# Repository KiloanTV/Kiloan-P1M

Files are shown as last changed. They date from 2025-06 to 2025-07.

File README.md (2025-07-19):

<div>
  <h1 align="center">Kiloan P1M V1</h1>

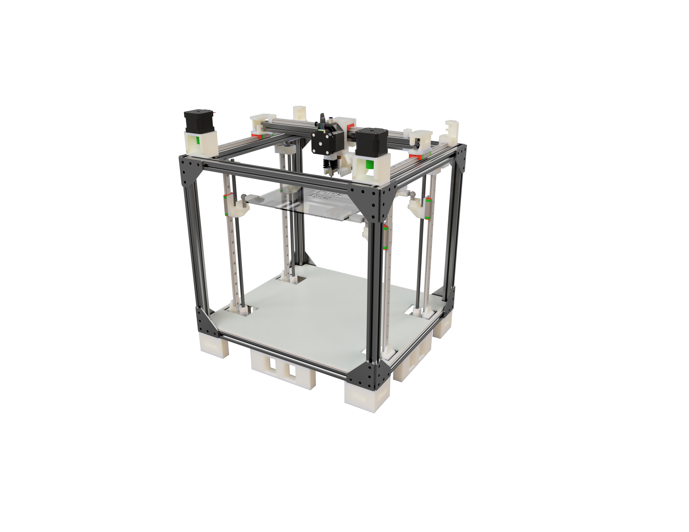
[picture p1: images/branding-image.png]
Kiloan-P1M
  

  <p align="center">
  <a href="https://hackclub.com/highway">
    
  </a>
  </p>
  <h1></h1>
  <p align="center">
    A custom 3D Printer, that is expandable, reliable and can be easily modified!
  </p>
</div>

<sub align="center">This work is licensed under the
[MIT License](https://mit-license.org).
</sub>

## Table of Contents

- [About](#about)
- [Pictures](#pictures)
- [Bill of Materials](#bill-of-materials)

# About

I bought a 3D printer exactly a year ago, and since then, the whole thing has been on my mind. From modeling to the finished part, whether it's spare parts or small gifts. I received an email from GitHub Education informing me about Highway by Hackclub, and after stumbling across it again, I started designing a Corexy 3D printer. Admittedly, it's a bit overkill, but that makes the whole thing even better and allows for many updates. After Highway, I plan to perfect this printer and turn it into a 3D printing/laser cutting combo.

# Pictures

zy

full-printer

# Bill of Materials

|Titel |Quantity|Price in Euro|Shipping costs|Link |
|---|---|---|---|---|
|Aluminium Extrusion 400mm |5 |€13,53 | |https://www.aluxprofil.de/aluminium-nutprofil-2020-v-slot/a3663 |
|Aluminium Extrusion 390mm |4 |€10,53 | |https://www.aluxprofil.de/aluminium-nutprofil-2020-v-slot/a3663 |
|Aluminium Extrusion 350mm |4 |€9,45 | |https://www.aluxprofil.de/aluminium-nutprofil-2020-v-slot/a3663 |
|Aluminium Extrusion 310mm |2 |€4,18 | |https://www.aluxprofil.de/aluminium-nutprofil-2020-v-slot/a3663 |
|Aluminium Extrusion 370mm |1 |€2,50 | |https://www.aluxprofil.de/aluminium-nutprofil-2020-v-slot/a3663 |
|Aluminium Extrusion 80mm (2x40mm) |2 |€1,08 | |https://www.aluxprofil.de/aluminium-nutprofil-2020-v-slot/a3663 |
|Aluminum L-connector plate 60x60 |16 |€19,48 | |https://www.aluxprofil.de/aluminium-l-verbinderplatte-60x60/a3809 |
|Aluminum connector plate 20x80 |4 |€3,39 | |https://www.aluxprofil.de/aluminium-verbinderplatte-20x80/a3804 |
|Washers |4 |1,60€ |5,95€ |https://www.reichelt.de/de/de/shop/produkt/unterlegscheiben_5_3_mm_100_stueck-65765 |
|Miniature ball bearing 698 2RS 8x19x6 mm|4 |2,95€ |2,49€ |https://www.kugellager-express.de/miniatur-kugellager-698-2rs-8x19x6-mm |
|5mm - 8mm Flexible coupling 18x25mm |4 |6,19€ | |https://www.amazon.de/Kupplung-Flexible-Kupplungen-Durchmesser-Maschine/dp/B06WRN9479 |
|350mm linear guides + carriage |4 |53,99€ | |https://www.amazon.de/CNCMANS-Linearf%C3%BChrungen-Schienenf%C3%BChrung-Gleitbl%C3%B6cke-Linearlager/dp/B0BPS1LFH9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 |
|M3 x 12mm Screws |1 pack  |1,69€ |5,90€ |https://www.schraubenking-shop.de/M3-x-12mm-Linsenkopfschrauben-TX-DIN7985-Edelstahl-A2-P004389 |
|M3 Nuts |1 pack  |1,43€ | |https://www.schraubenking-shop.de/M3-Sechskantmuttern-DIN934-Edelstahl-A2-P000447 |
|Nema 17 Steppers |2 x 3 |32,14€ |6,08€ |https://www.omc-stepperonline.com/de/3-stueck-e-serie-nema-17-bipolar-42-ncm-59-49-oz-in-1-5a-42x42x38mm-4-draehte-3-17he15-1504s |
|M3 x 8mm Screws |1 pack  |1,97€ | |https://www.schraubenking-shop.de/M3-x-8mm-Linsenkopfschrauben-TX-DIN7985-Edelstahl-A2-P004281 |
|TR8x4 trapezoidal thread spindle 400mm  |4 |38,40€ | |https://3d-druckershop.com/p/tr8x4-trapezgewindespindel-edelstahl-8mm-laenge-400mm-kaufen |
|TR8x4 trapezoidal thread nut |4 |11,80€ |5,99€ |https://3d-druckershop.com/p/tr8x4-trapezgewindemutter-messing-kaufen |
|M3 x 8mm threaded pin |1 pack  |0,74€ | |https://www.schraubenking-shop.de/M3-x-8mm-Gewindestift-Kegelkuppe-DIN913-Edelstahl-A2-P005088 |
|Miniature ball bearing 608 2RS 8x22x7 mm|4 |2,76€ | |https://www.kugellager-express.de/miniatur-kugellager-608-2rs-8x22x7-mm |
|M5 x 16mm Screws |1 pack  |0,96€ | |https://www.schraubenking-shop.de/M5-x-16mm-Linsenkopfschrauben-TX-DIN7985-Edelstahl-A2-P004003 |
|225mm x 225mm hotbed + aluminium plate  |1 |29,99€ |5,79€ |https://www.3djake.de/elegoo/heizbett-8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 |
|300 mm linear rail guide + carriage |1 x 2 |36,99€ | |https://www.amazon.de/Linearschienenf%C3%BChrung-Lagerstahl-Gleitf%C3%BChrung-Gleitbl%C3%B6cken-CNC-Maschine/dp/B09ZPHPB5F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 |
|MGN12H 350mm linear guide |1 |16,02€ | |https://www.amazon.de/CNCMANS-Linearf%C3%BChrung-Schienenf%C3%BChrung-CNC-Maschine-automatische/dp/B0BG29BQ6H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 |
|M5 angle joint |4 |7,56€ |1,80€ |https://www.ebay.de/itm/124341250847?itemid=124341250847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 |
|M3 x 40mm Screws |1 pack  |3,07€ | |https://www.schraubenking-shop.de/M3-x-40mm-Linsenkopfschrauben-PH-DIN7985-Stahl-verzinkt-FKL48-P002826 |
|Flanged ball bearings |12 |25,99€ | |https://www.kugellager-express.de/miniatur-flanschkugellager-f-695-2rs-5x13x4-mm |
|GT2 pulley idler |2 |5,10€ | |https://www.roboter-bausatz.de/p/gt2-riemenscheibe-idler-20-zaehne-5mm-bohrung-fuer-6mm-schwarz |
|GT2 pulley |2 |1,98€ | |https://www.roboter-bausatz.de/p/gt2-riemenscheibe-20-zaehne-5mm-bohrung-fuer-6mm-riemen |
|M5 x 40mm Screws |1 pack  |1,31€ | |https://www.schraubenking-shop.de/M5-x-40mm-Linsenkopfschrauben-TX-DIN7985-Edelstahl-A2-P004001 |
|M5 x 30mm Screws |1 pack  |1,10€ | |https://www.schraubenking-shop.de/M5-x-30mm-Linsenkopfschrauben-TX-DIN7985-Edelstahl-A2-P004403 |
|Dual Gear Extruder BMG Clone |1 |19,95€ | |https://www.roboter-bausatz.de/p/dual-gear-extruder-bmg-klon-fuer-1.75mm-filament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 |
|Nema 17 Stepper 23mm for extruder |1 |6,53€ | |https://www.omc-stepperonline.com/de/e-serie-nema-17-bipolar-1-8deg-17ncm-24-07oz-in-1a-42x42x23mm-4-draehte-17he08-1004s |
|Bambu X1C Hotend |1 |36,99€ | |https://eu.store.bambulab.com/products/bambu-hotends?id=49242578223452 |
|BL Touch |1 |39,90€ | |https://www.3dprima.com/de/parts/bltouch_23625_4704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 |
|Part cooling fan 5015 24V |1 |1,95€ | |https://www.roboter-bausatz.de/p/radialluefter-5015-24v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 |
|BigTreeTech SKR Mini E3 V3 |2 |0,00€ | |have it already |
|powersupply |1 |45,99€ | |https://www.amazon.de/MEISHILE-Schaltnetzteil-Stromversorgung-Transformator-Spannungswandler/dp/B0DJQRZ24G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 |
|Mainboard fan |2 |0,00€ | |have it already |
|T-Nut 6 M5 for aluminium extrusions |200 |10,09€ | |https://de.aliexpress.com/item/1005007843353724.html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 |
|M5 x 8mm |2 packs |5,62€ | |https://www.schraubenking-shop.de/M5-x-8mm-Linsenkopfschrauben-PH-DIN7985-Stahl-verzinkt-FKL48-P003609 |
|GT2 6mm belt |5 Meter |4,84€ | |https://de.aliexpress.com/item/32921042288.html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|
|||555,73€ or 647,60 USD|||

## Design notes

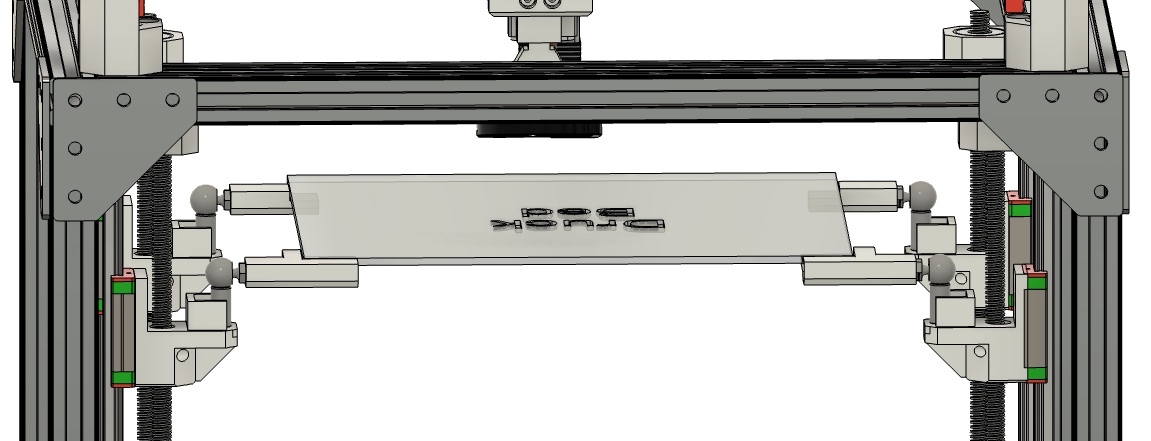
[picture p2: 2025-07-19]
images/bed-system.jpeg

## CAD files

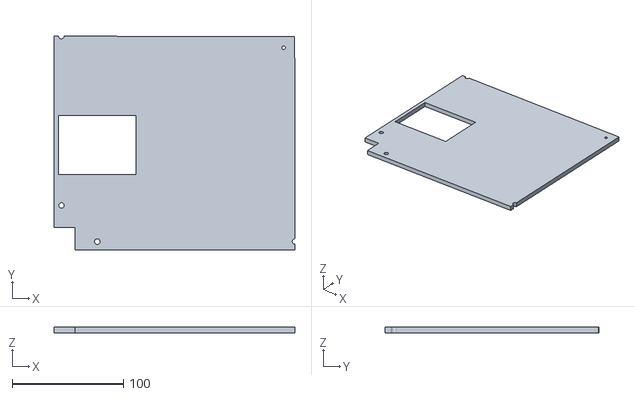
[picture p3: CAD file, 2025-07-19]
hardware/misc/cover2.stl
217.0 x 192.5 x 5.00

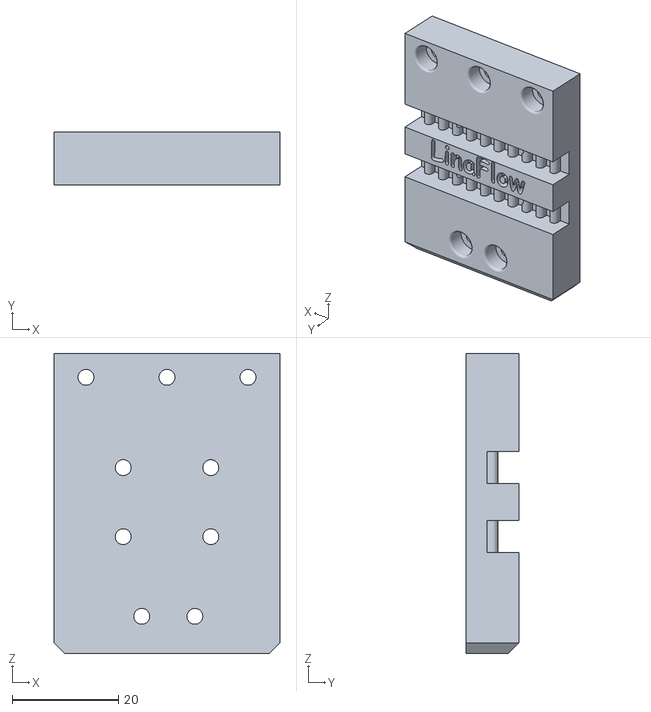
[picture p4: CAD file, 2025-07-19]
hardware/printhead/printhead-frontplate.stl
42.5 x 10.0 x 56.5

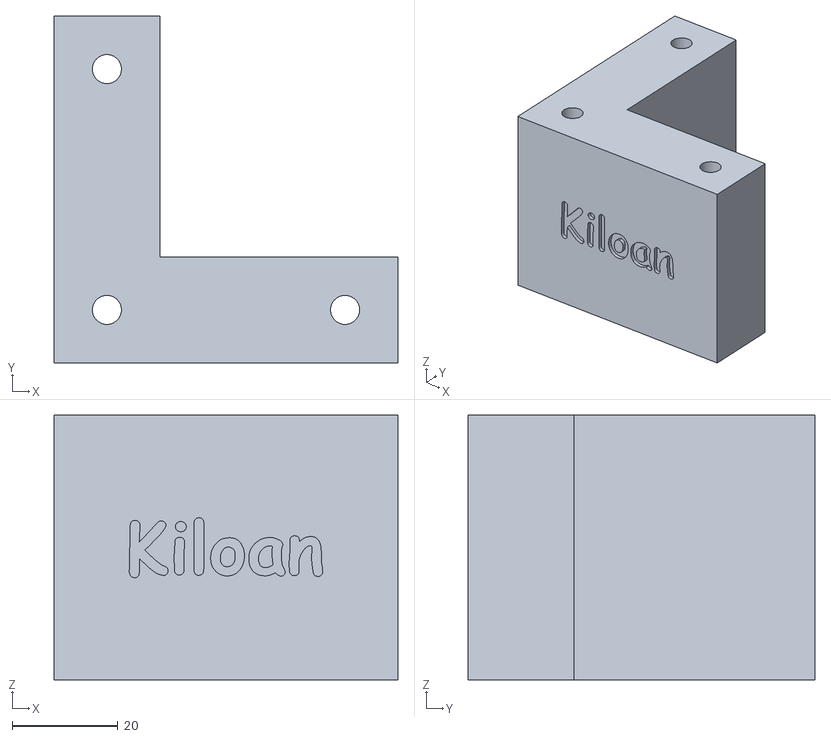
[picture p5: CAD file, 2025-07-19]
hardware/misc/feet8.stl
65.0 x 65.5 x 50.0

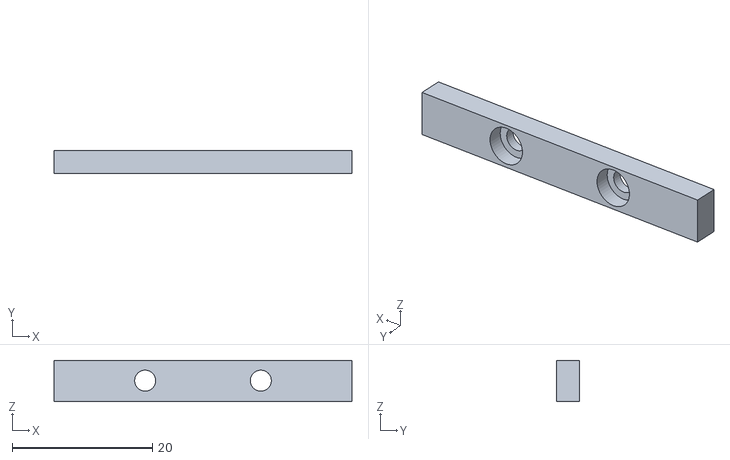
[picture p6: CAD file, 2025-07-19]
hardware/printhead/printhead-belt-con.stl
42.5 x 3.25 x 5.90

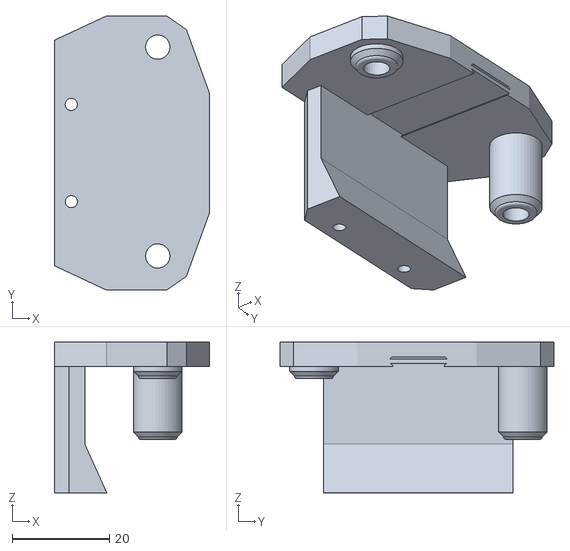
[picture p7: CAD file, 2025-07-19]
hardware/x/x-sidemount-top.stl
32.0 x 56.4 x 31.0

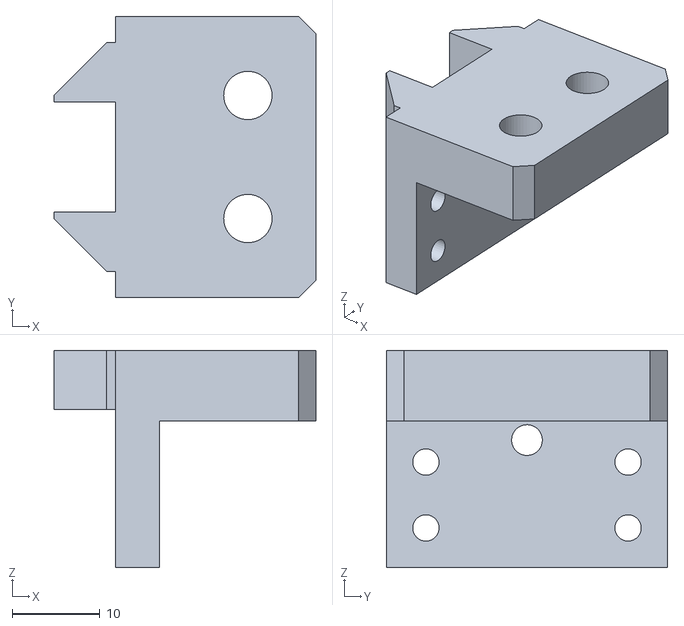
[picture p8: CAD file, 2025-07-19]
hardware/z/z-top-alucon.stl
29.8 x 32.0 x 24.7

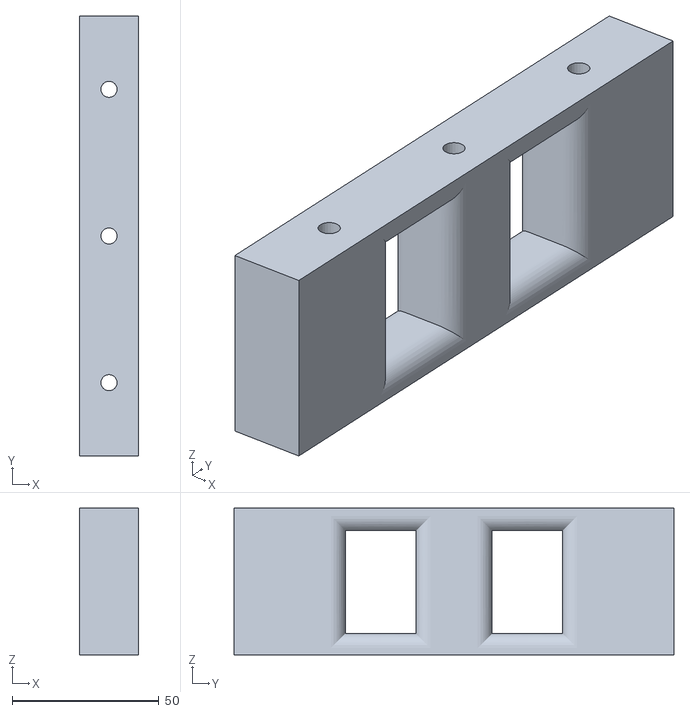
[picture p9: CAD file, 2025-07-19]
hardware/misc/feet6.stl
20.0 x 150.0 x 50.0

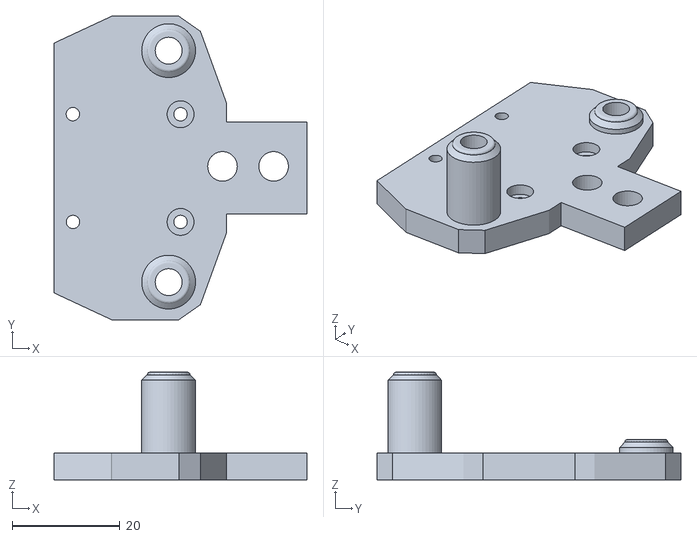
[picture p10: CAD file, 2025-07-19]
hardware/x/x-sidemount-buttom.stl
47.0 x 56.4 x 20.0

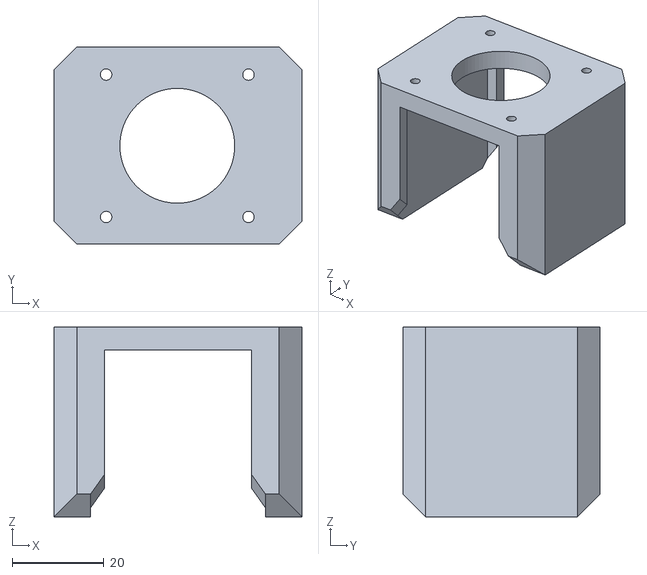
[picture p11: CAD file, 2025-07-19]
hardware/y/xy-nema17-base-top.stl
54.0 x 43.0 x 41.3

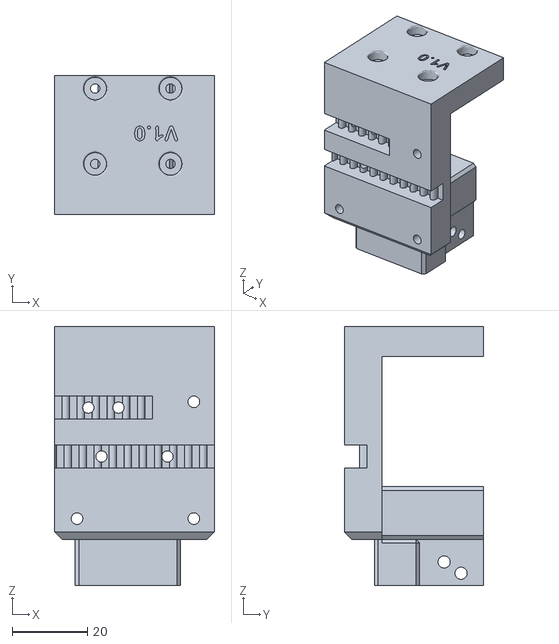
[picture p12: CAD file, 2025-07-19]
hardware/printhead/printhead-mount-back.stl
42.5 x 37.0 x 68.7

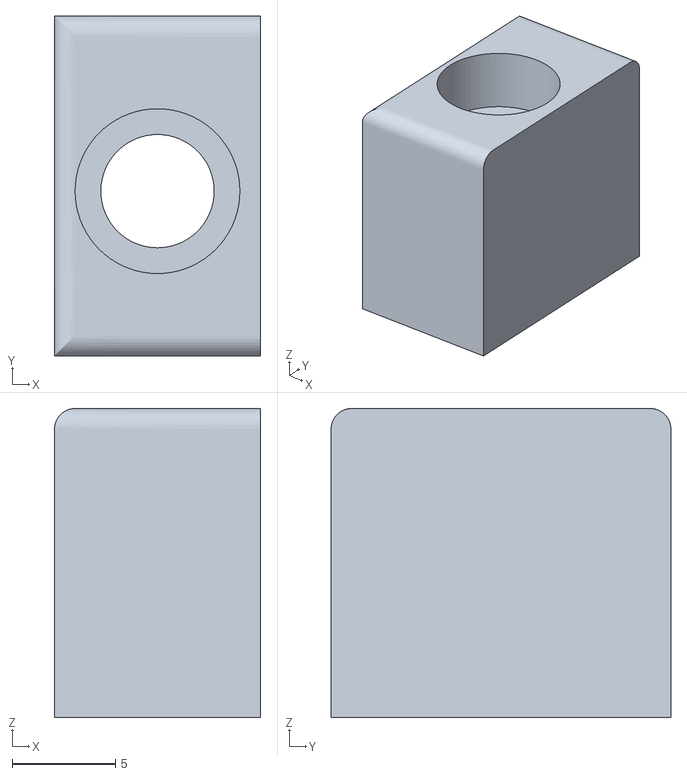
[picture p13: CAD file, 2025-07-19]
hardware/x/x-endstop.stl
10.0 x 16.5 x 15.0

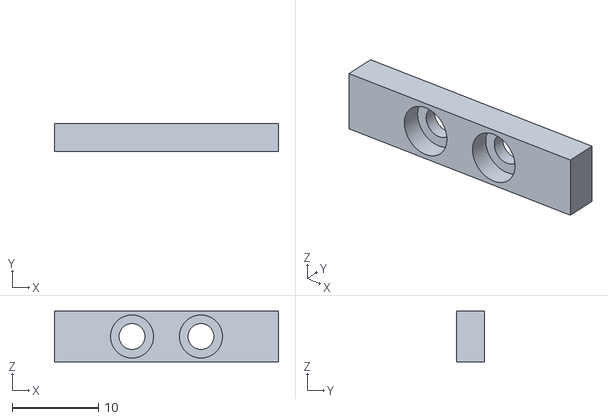
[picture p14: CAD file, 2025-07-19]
hardware/printhead/printhead-belt-con-front-left.stl
26.0 x 3.25 x 5.90

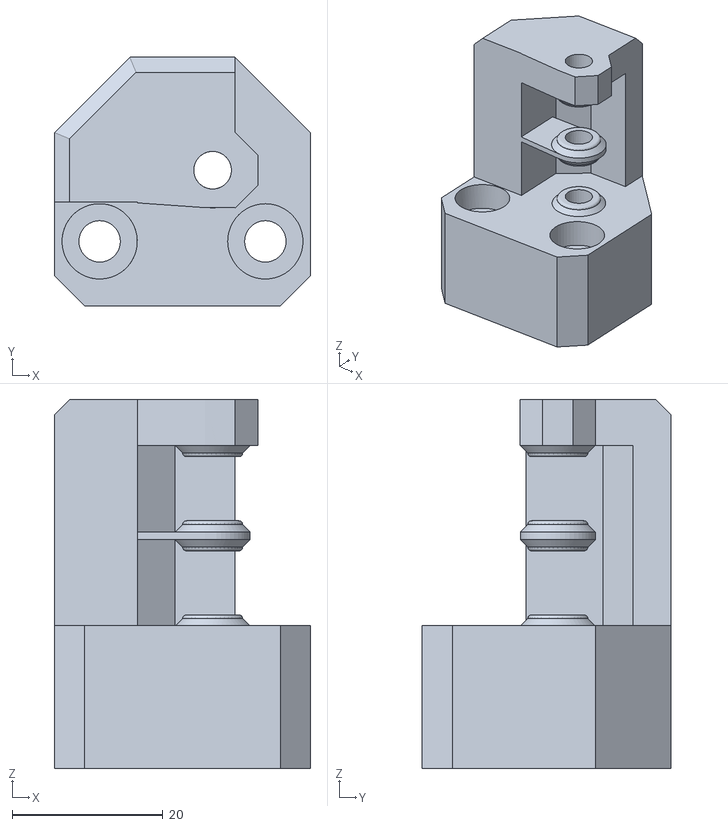
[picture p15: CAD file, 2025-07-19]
hardware/y/xy-bearing-ending-mounts.stl
34.0 x 33.0 x 49.0

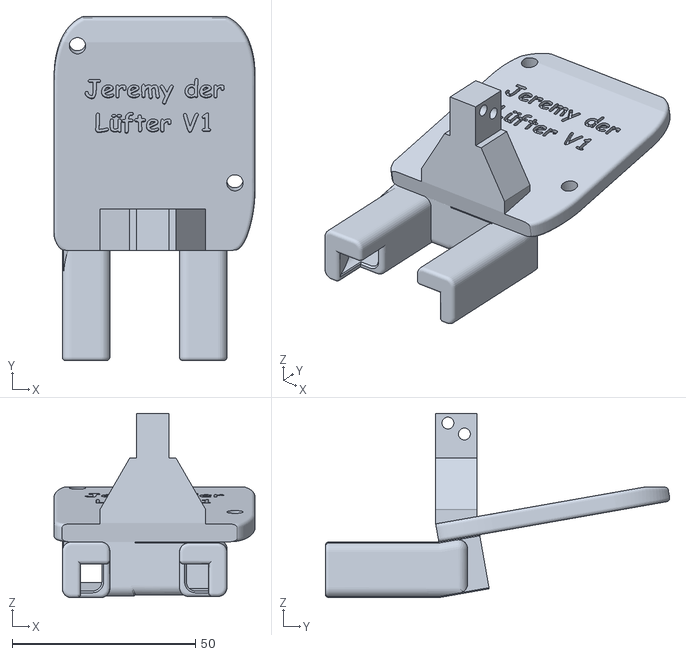
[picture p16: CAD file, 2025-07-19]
hardware/printhead/part-cooling-fan-mount.stl
54.9 x 94.1 x 50.3

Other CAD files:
hardware/printhead/printhead-belt-con-front-right.stl
hardware/misc/feet2.stl
hardware/misc/feet5.stl
hardware/misc/feet7.stl
hardware/Kiloan P1M V1.f3z
hardware/misc/cover-connector.stl
hardware/misc/cover1.stl
hardware/misc/cover3.stl
hardware/misc/cover4.stl
hardware/misc/feet1.stl
hardware/misc/feet3.stl
hardware/misc/feet4.stl
hardware/printhead/bambu-hotendadapter-V6.stl
hardware/printhead/printhead-belt-con2.stl
hardware/x/x-endstop (1).stl
hardware/x/x-sidemount-buttom (1).stl
hardware/x/x-sidemount-top (1).stl
hardware/y/xy-bearing-ending-mounts (1).stl
hardware/y/xy-nema17-base (1).stl
hardware/y/xy-nema17-base-top (1).stl
hardware/y/xy-nema17-base.stl
hardware/z/bedmount (1).stl
hardware/z/bedmount (2).stl
hardware/z/bedmount (3).stl
hardware/z/bedmount.stl
hardware/z/z-alucon-buttom (1).stl
hardware/z/z-alucon-buttom (2).stl
hardware/z/z-alucon-buttom (3).stl
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

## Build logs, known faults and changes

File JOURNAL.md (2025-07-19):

---
title: "Kiloan P1M"
author: "Kian Lorenz"
description: "Custom CoreXY printer for 3D Printing"
created_at: "2025-06-15"
---

**Total time spent: 42hrs**

# June 15th - Planning the concept (0.5hrs)

After I had a rough idea of what I wanted to build, I wrote down my ideas. The goal is to design an inexpensive and simple CoreXY printer and construct it so that the print head can be replaced with a laser. I've had this idea for a few months now and am now taking this opportunity to implement it. The printer should be usable with and without an enclosure.

- Aluminum frame (2020)
- CoreXY
- should be easily scalable
- swapable toolheads (FDM and Laser)
- autoleveling
- emergency stop
- full enclosure
- Nema 17 Motors if possible

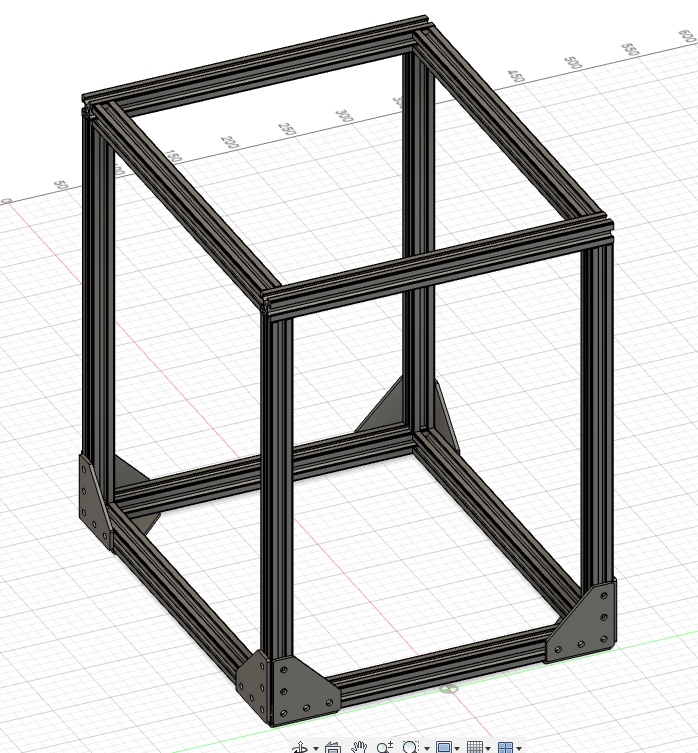
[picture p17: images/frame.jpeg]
Frame Idea


# June 15th - Frame and Z-Axis (10hrs)

I learned from YouTube how a typical CoreXY printer is constructed. Then I started designing in Fusion360. After the frame, I continued with the Z-axis. In my mind, this design should work well and print semi-well (i am learning cad with this project). The system uses a trapezoidal lead screw and the corresponding TR8x4 trapezoidal lead nut to move the Z-axis up and down, attached to linear guides. Nema 17 motors are used because they are inexpensive in my area.

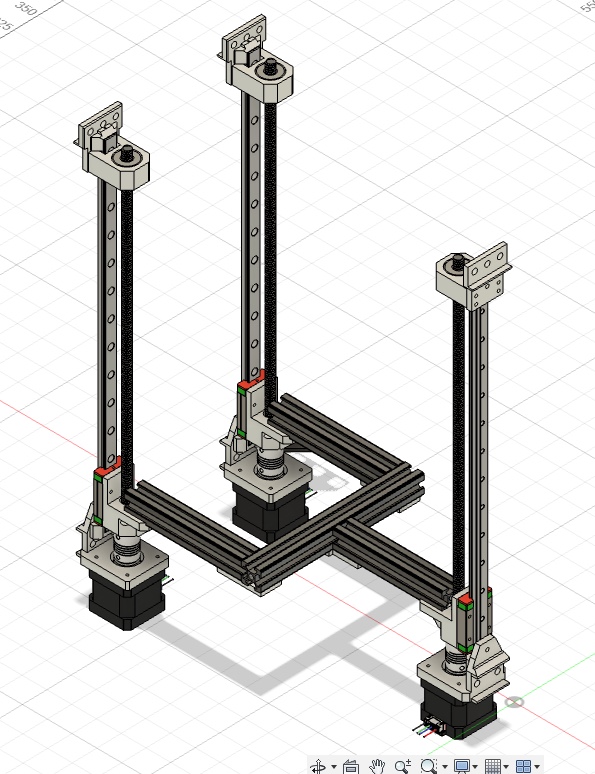
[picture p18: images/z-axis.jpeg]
z-axis


A 3D printed holder is screwed into the aluminum extrusion at all three points at the top. The linear rail is then attached to this holder. Another holder is screwed on and fitted with a ball bearing so that the trapezoidal lead screw is held and can rotate freely.

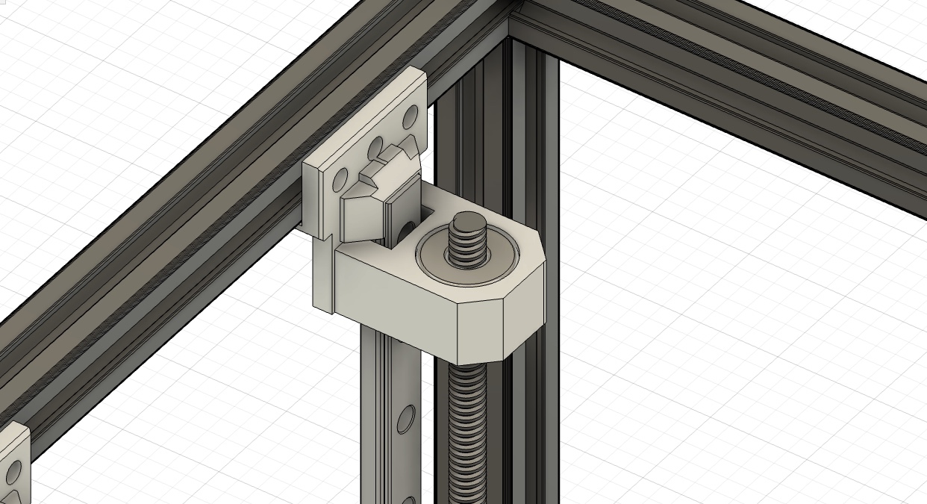
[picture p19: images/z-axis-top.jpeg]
z-axis-top


Below, a 3D-printed holder is screwed to the aluminum extrusion where the linear rail and motor are attached. The trapezoidal lead screw is attached to the motor via a 5mm to 8mm coupling, and the weight is distributed across the motor housing via a ball bearing with a washer to prevent excessive strain on the shaft. On the carriage, which sits on the linear rail, there is another 3D-printed holder that holds the trapezoidal lead screw nut and onto which the aluminum extrusion frame is screwed, upon which the print bed is then placed.

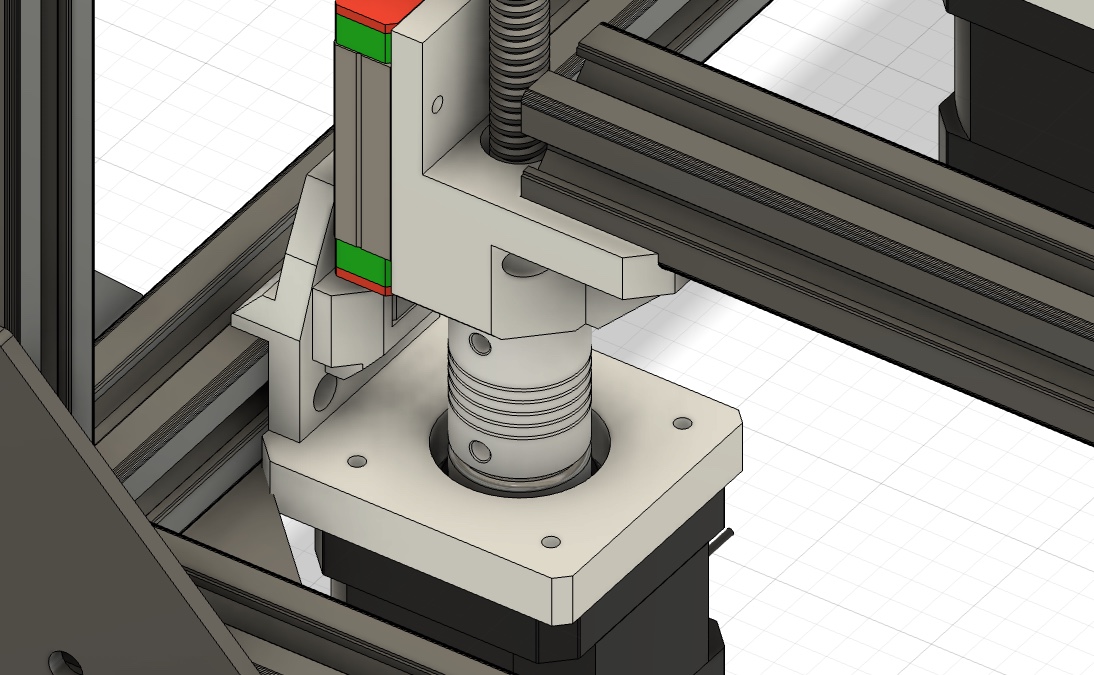
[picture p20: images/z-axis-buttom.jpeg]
z-axis-buttom


The aluminum extrusion frame for the print bed is held together with simple 3D printed plates.

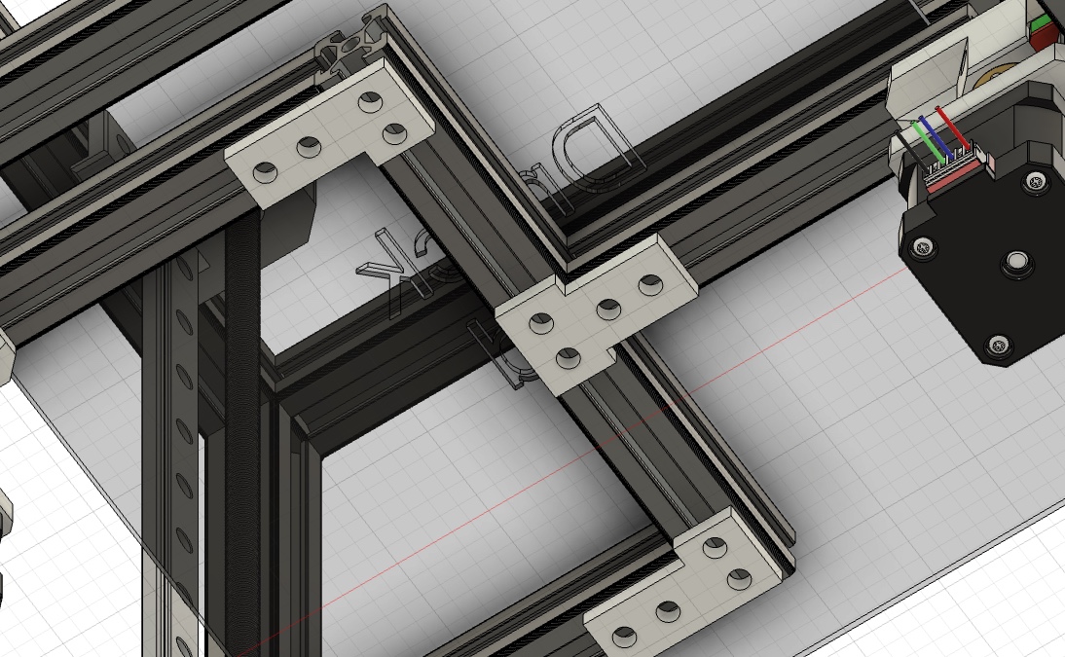
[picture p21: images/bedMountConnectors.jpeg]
BedFrame


# June 18th - XY-Axis (6.5hrs)

After a few school exams, I was finally able to move on to the remaining axes. The Y-axis already has two linear rails, and I've finished the 3D-printed mounts. These include space for screwing the two idler pulleys at two different heights for the two belt loops. I also learned today how the corexy system works exactly; YouTube was my best source of help.

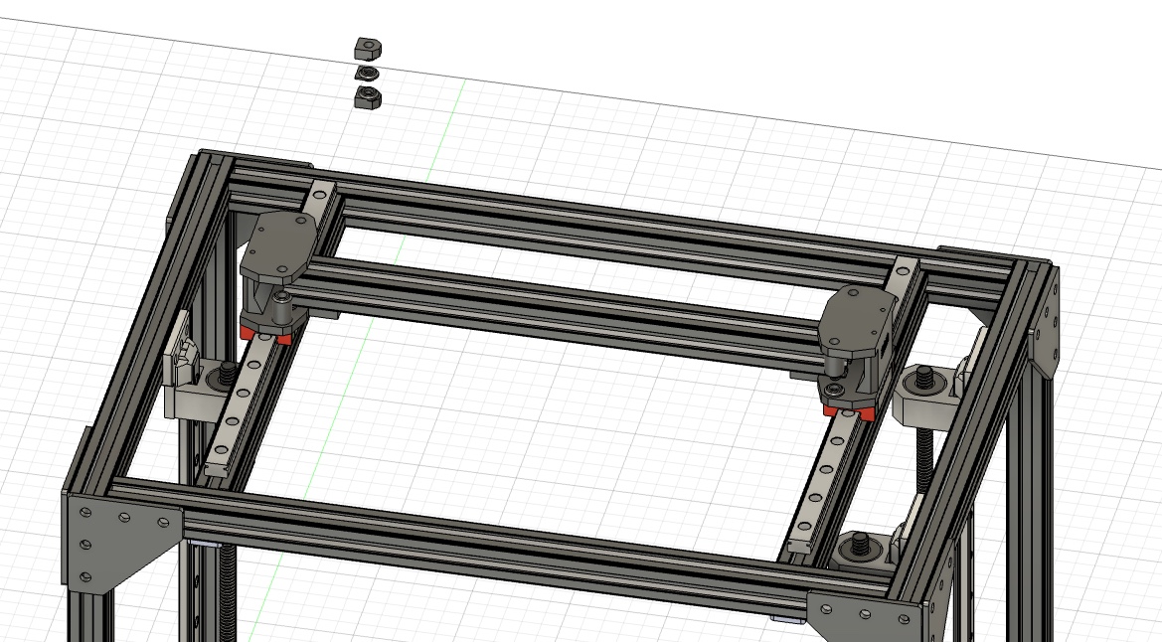
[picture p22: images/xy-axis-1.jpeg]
xy-axis-1


The entire CAD project looks like this so far.

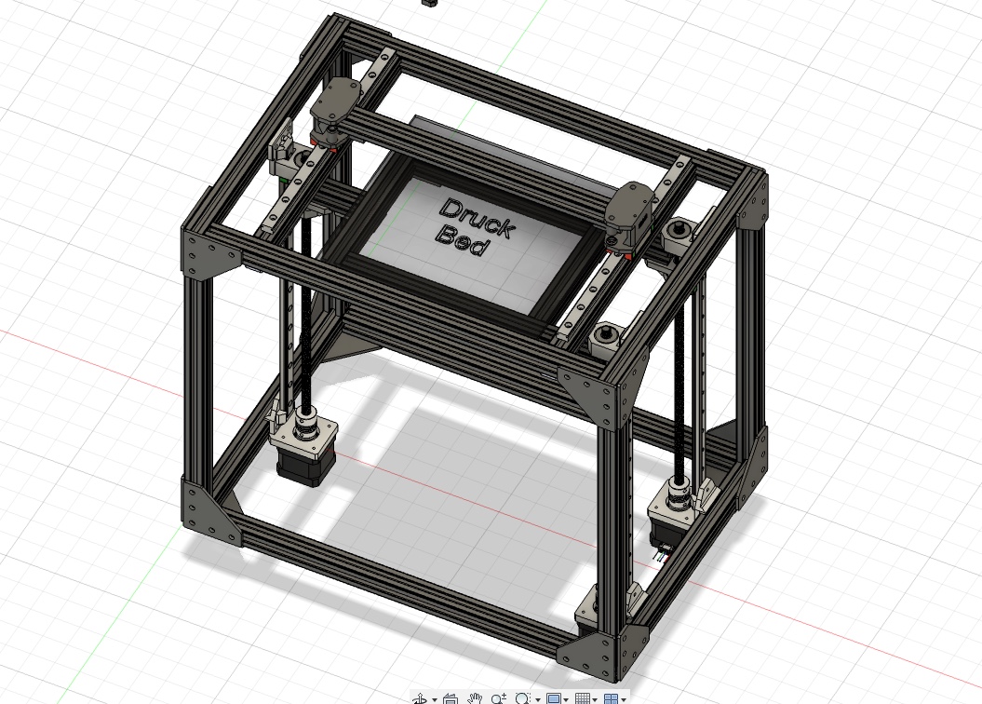
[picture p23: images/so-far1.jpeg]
so-far1


# June 22th - XY-Axis finis, learning and PrintHead (11.5hrs)

I've finally finished the end pieces for the XY axis. The middle plate holder is only loosely attached and, as mentioned, serves only as an intermediate piece to adjust the two idler pulleys to the correct distance. They've become a bit bulkier, but I think that gives the whole thing more stability and hopefully they will be easy to 3D print.

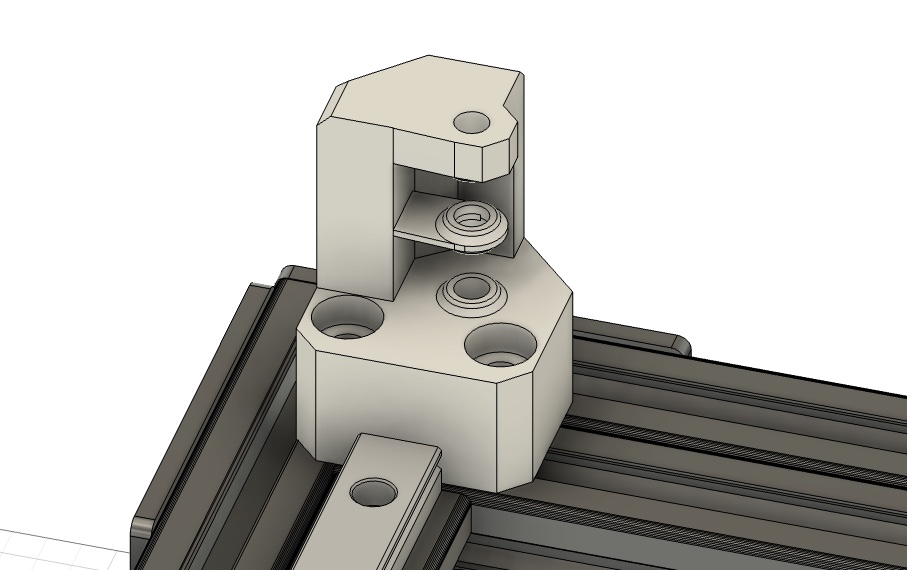
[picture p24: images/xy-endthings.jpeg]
xy-endthings


Next come the motor mounts, which are very simply made. You screw the NEMA 17 motor to the upper U-shaped part and attach it to the base plate. Now, with a bit of fiddling, you need to attach the base plate to the aluminum extrusions. Finally, you can screw the pulley to the motor shaft.

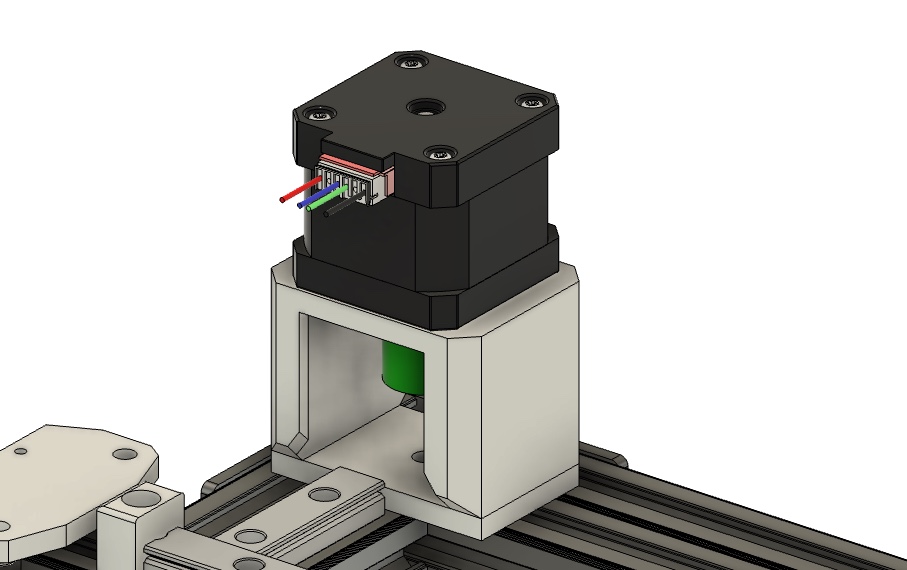
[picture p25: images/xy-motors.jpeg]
xy-motors


And now the XY axis looks like this. The Y axis needs to be adjusted because I didn't make any provision for leveling the print bed. So, I'll make the previously designed guides with linear rails at all four corners and add joints at all four corners to level the bed. Similar to a 5-axis 3D printer design.

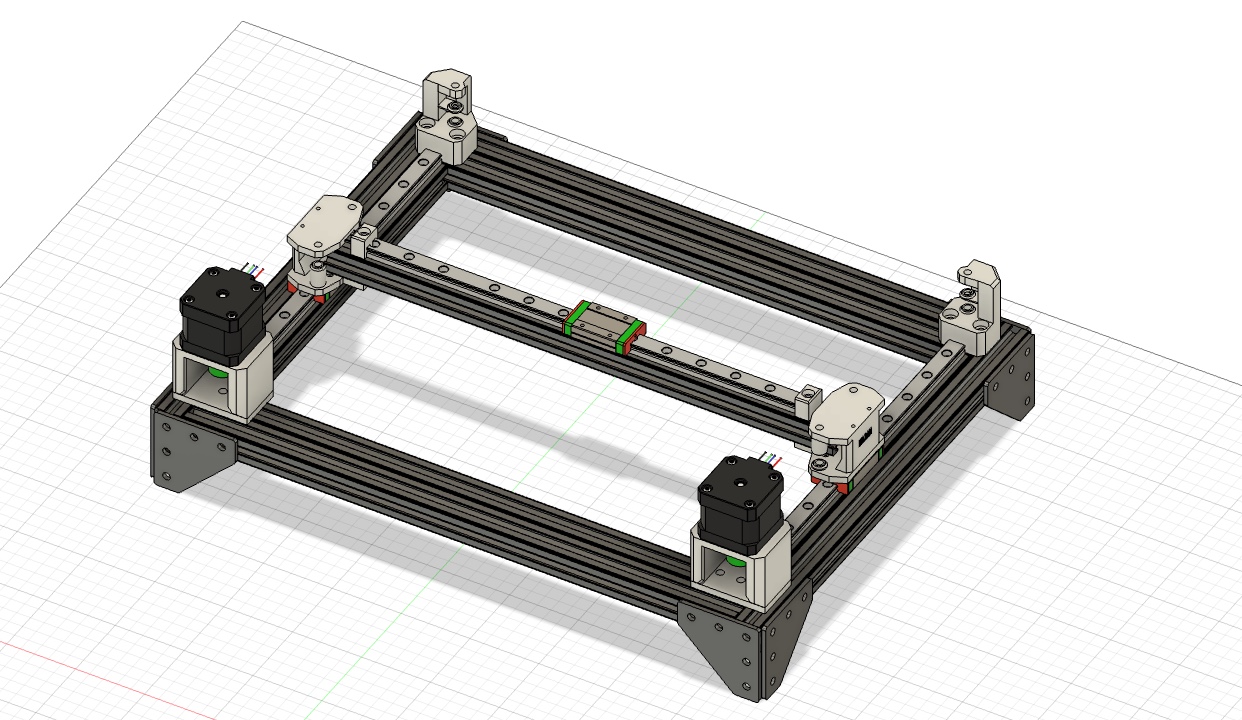
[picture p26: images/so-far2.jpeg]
so-far2


I've decided against the simple Creality CR10S extruder or the similar Ender 3 extruder. For direct extrusion, I'll use the dual gear BMG extruder or a cheap clone to minimize overall costs. I'll attach any NEMA 17 motor that's no longer than 48 centimeters to it, so I can enclose the printer later. With a small adapter, I can use the Bambu X1C hotend. For the electronics, I'd like to use a small control board on the print head, but I don't yet know how complicated that would be.

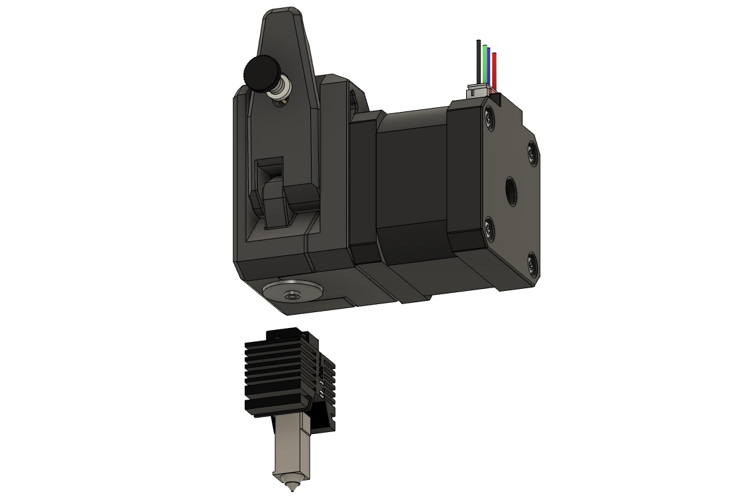
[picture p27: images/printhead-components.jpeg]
printhead-components


# July 5th - Printhead Mount and Printbed Redesign (9hrs)

After another exam period, I finally got back to work on this project. First, I modeled an adapter for the Bambu Lab hotend to mount it on the V6 universal mount.

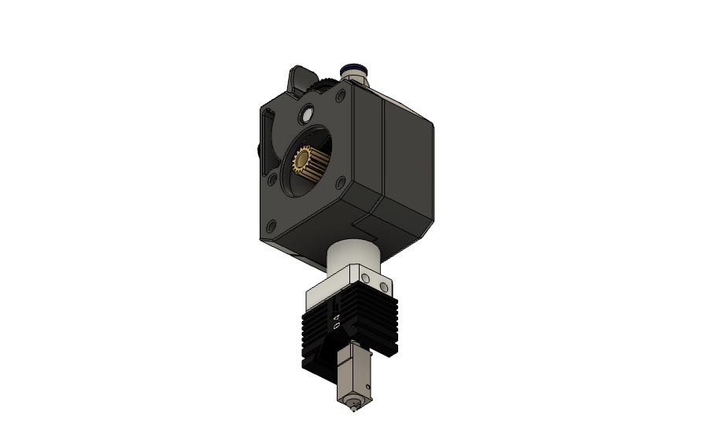
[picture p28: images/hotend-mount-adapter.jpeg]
hotend-mount-adapter


Next, I modeled a simple printhead mount to attach the existing components. This is screwed to the top of the linear guide carriage and runs around the entire x-axis to ensure stability. A counterplate is then screwed on from the other side, completing the basic system for mounting the print head.

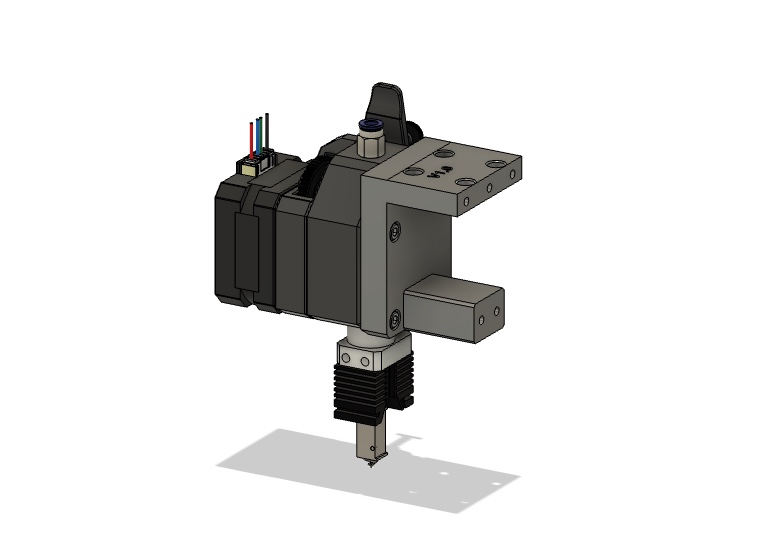
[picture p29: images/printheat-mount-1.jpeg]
printheat-mount-1


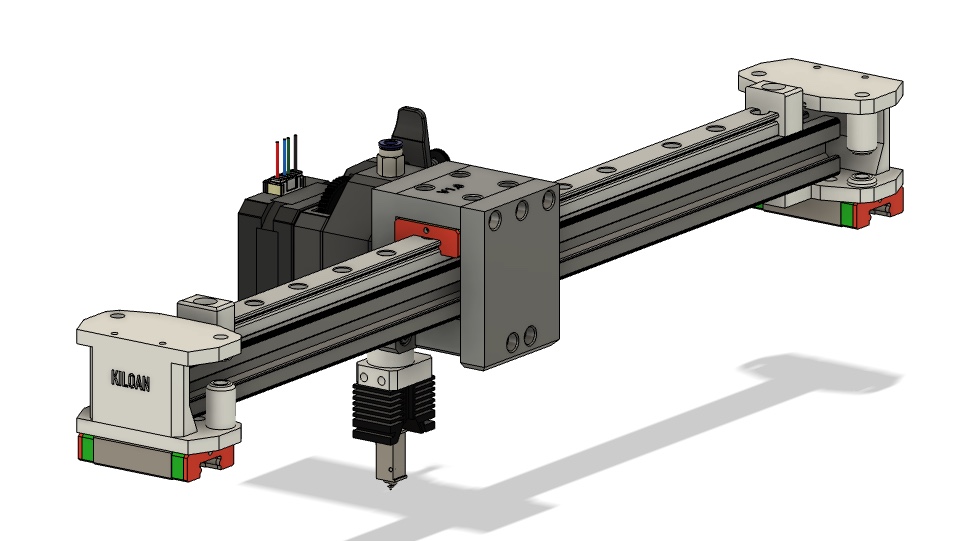
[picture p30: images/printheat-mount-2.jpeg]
printheat-mount-2


Next, I finally finished the print bed. It's attached to four corners with M5 ball joints, allowing the print bed to be adjusted at different heights. This allows for auto-leveling of the printer. Simple adapters are attached to the ball joints, which can be adjusted depending on the printbed size. It's important that the printbed is a combination with an aluminum plate; the plate can be attached to the adapter with clamps. The material should be at least ASA for heat resistance.

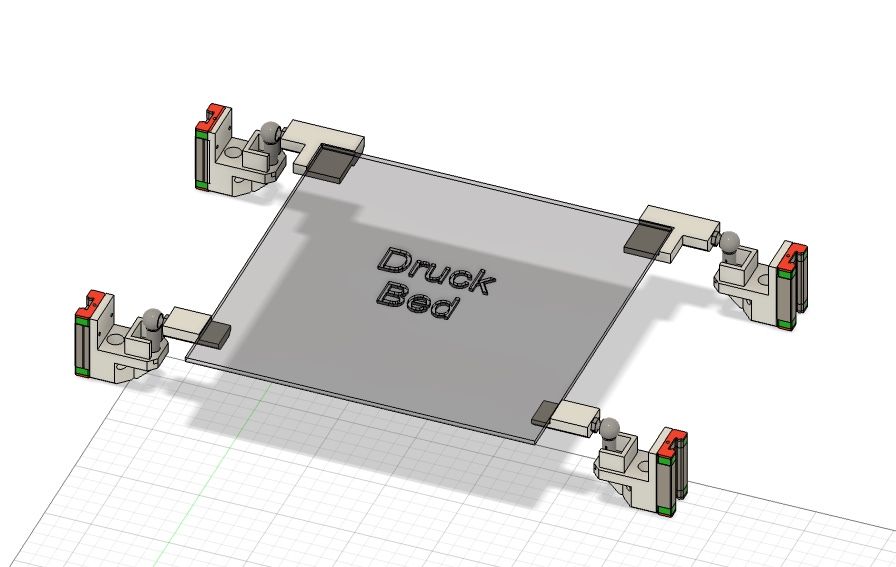
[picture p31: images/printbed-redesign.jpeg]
printbed-redesign


I also added another motor with a linear rail and carriage to implement the aforementioned bed leveling. The base frame made of aluminum extrusions was also slightly adjusted in width so that the printhead can reach all corners of the print bed and also to ensure the mobility of the Z-axis. I also decided against my wish to have a small circuit board on the print head to minimize cables, as I don't have enough time for it, and the main board to control the printer, including the motors, sensors, fans, and hotend, and to communicate with Klipper, is currently only in the planning stages.

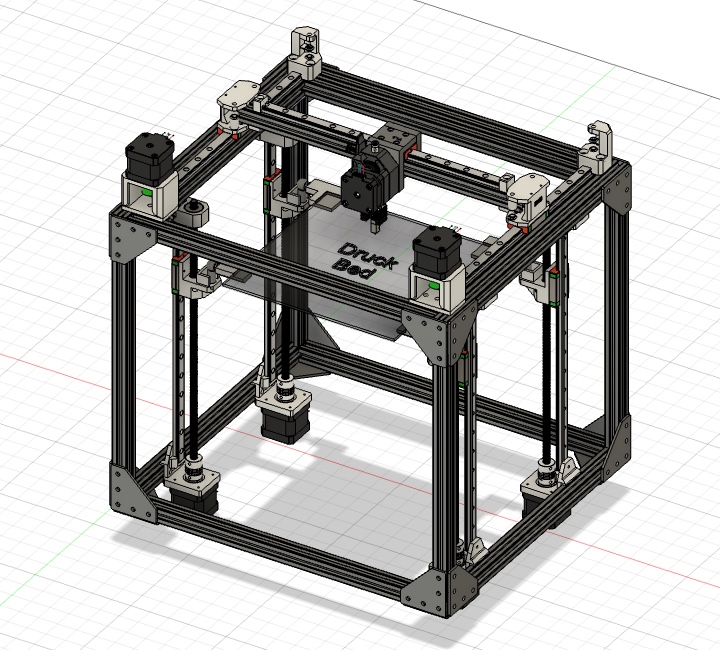
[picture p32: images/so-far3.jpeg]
so-far3


# July 6th - Printhead and finally feet! (4.5hrs)

Finally, the printer has feet to stand on. On my to-do list for the final design changes is the enclosure for printing materials like ABS and ASA, and, more importantly, for using a slightly more powerful laser. The mount and laser will be modeled and selected based on the controller PCB design, as the 3D printer concept needs to be finalized first.

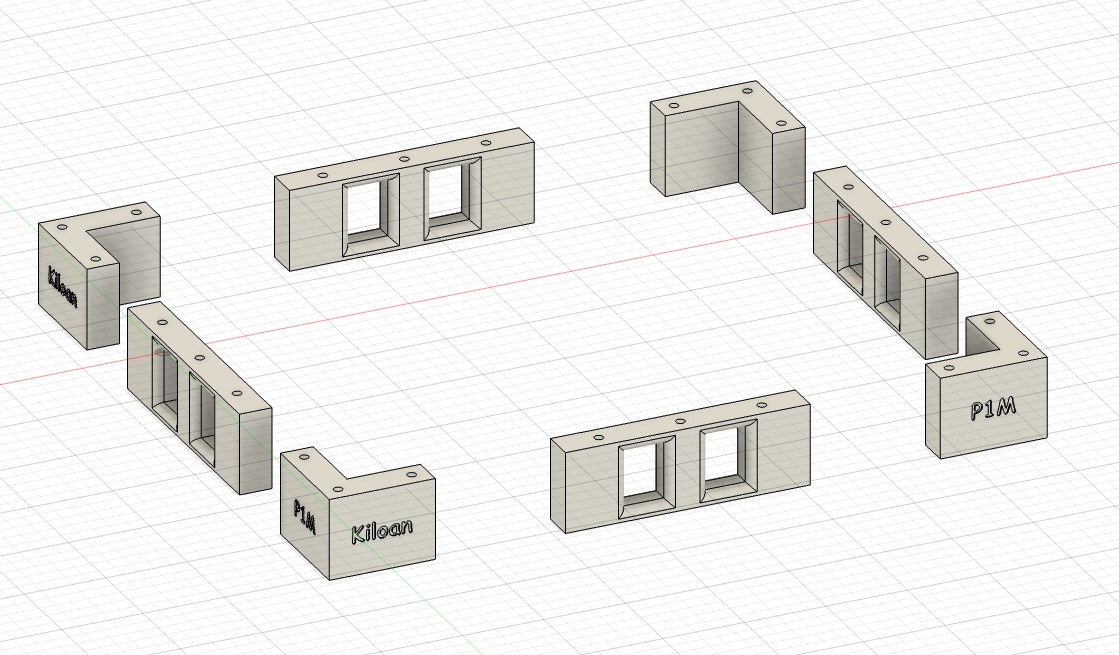
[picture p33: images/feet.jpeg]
feet


The final changes to the printheat are complete. Now there's a BL touch sensor for auto-leveling and, of course, the parts cooling fan with a somewhat awkward mount so that the aluminum extrusions don't get in the way and the print head can reach everywhere. Two stoppers are attached to the ends of the linear rail to hold the linear rail carriage at the ends.

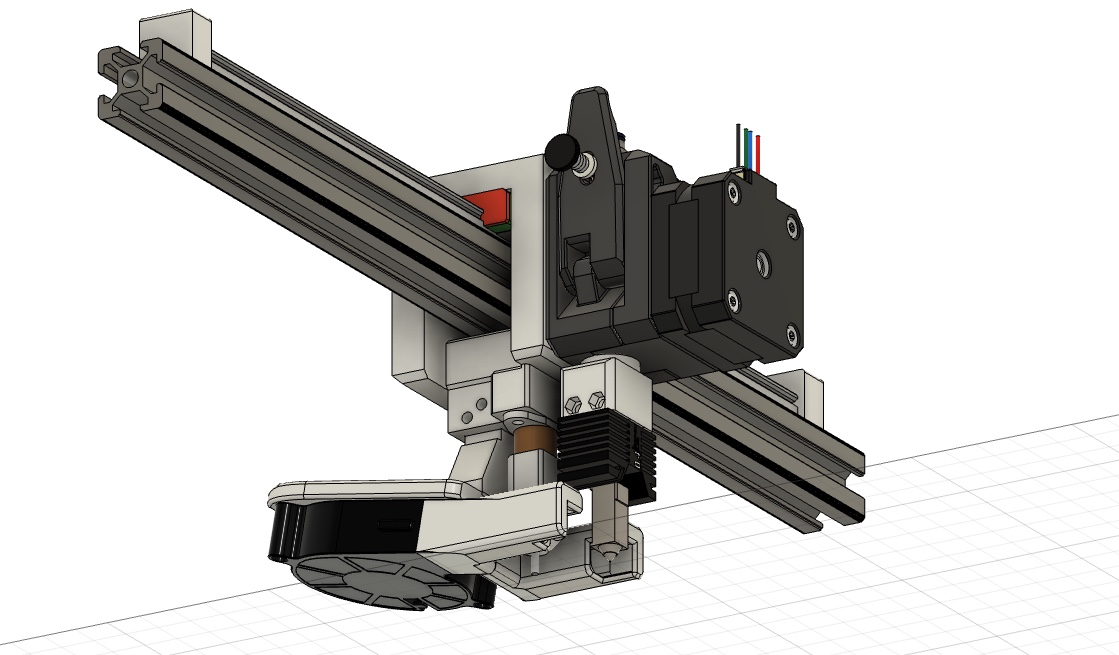
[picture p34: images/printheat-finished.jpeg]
printheat-finished


Here are some CAD images for the new x-axis system and the bed in combination with the finished printhead.

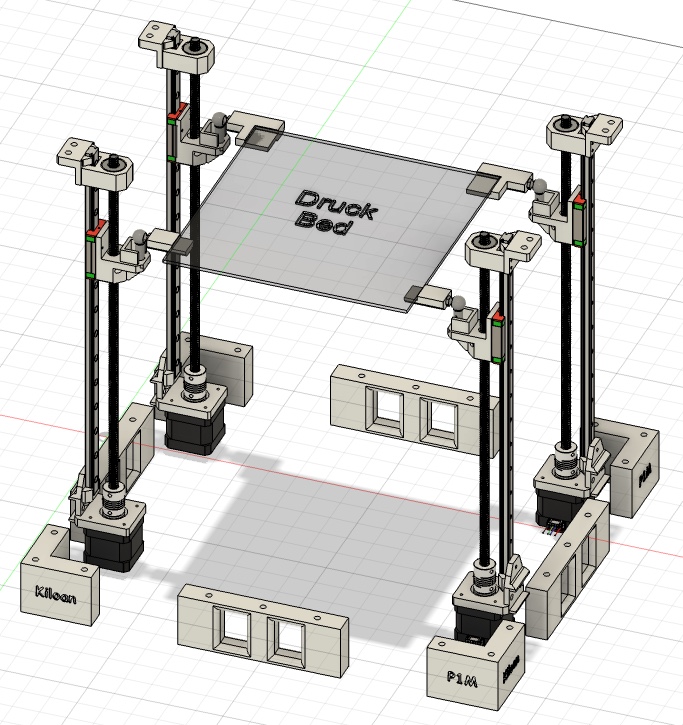
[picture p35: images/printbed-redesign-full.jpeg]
printbed-redesign-full


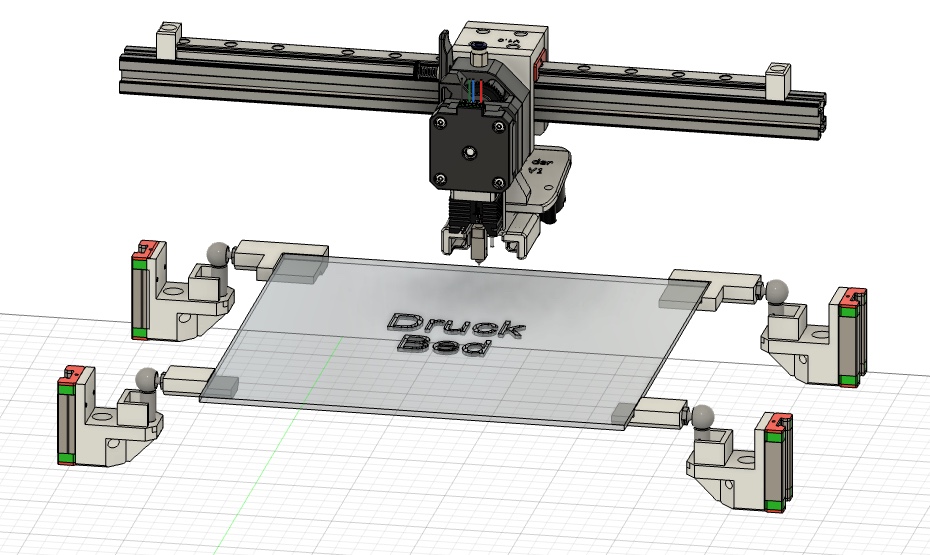
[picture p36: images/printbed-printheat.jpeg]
printbed-printheat


Here it is again in combination with the aluminum frame and the feet, which of course have the name of the project engraved on them.

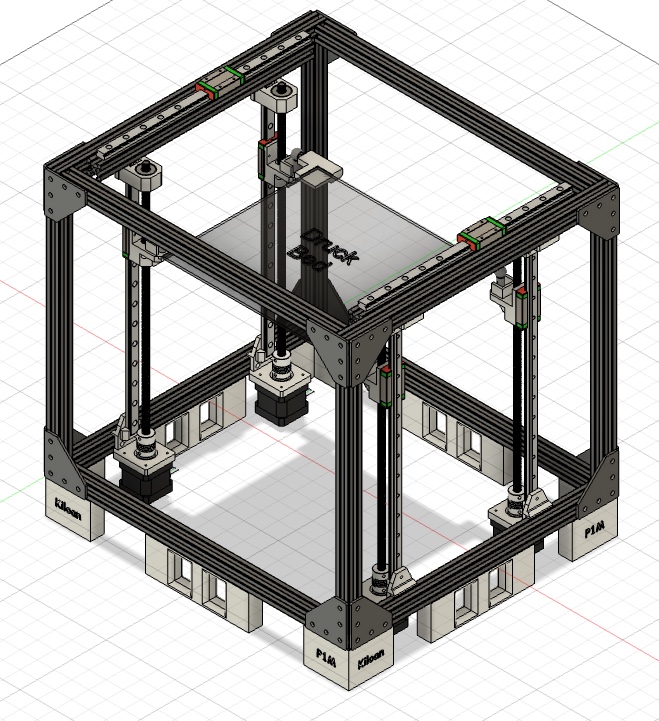
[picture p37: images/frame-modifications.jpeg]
frame-modifications


And finally, the basic design of the 3D printer is complete. Now it's time to design the motherboard for the printer. Next comes the laser selection and the modeling of the mount and enclosure. I actually wanted to finish this project a long time ago, but I don't have as much time as I thought. I'd like to realize other projects, but time is, as always, the issue.

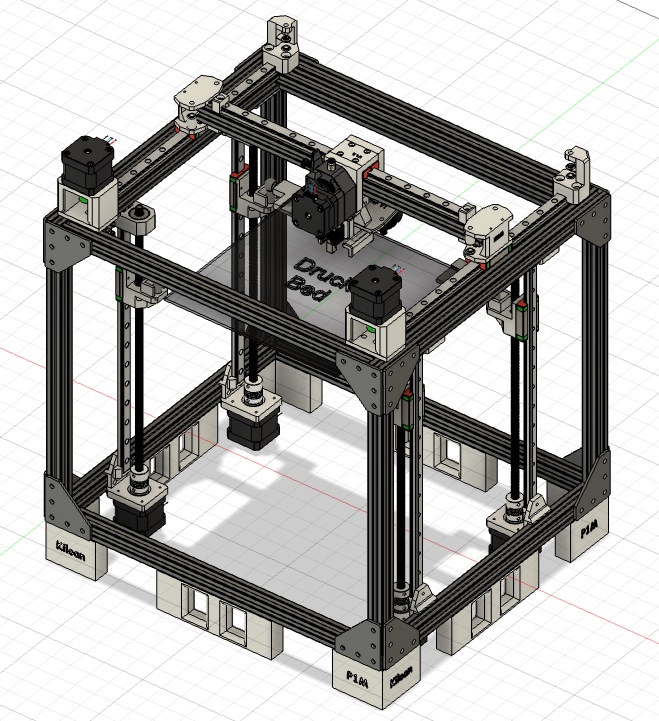
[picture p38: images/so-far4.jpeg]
so-far4


# July 15th - Error correction (1.5hrs)

I took another look at the design and realized that there was no way to attach the belt to the printhead. That's now there, too, albeit a bit impractical.

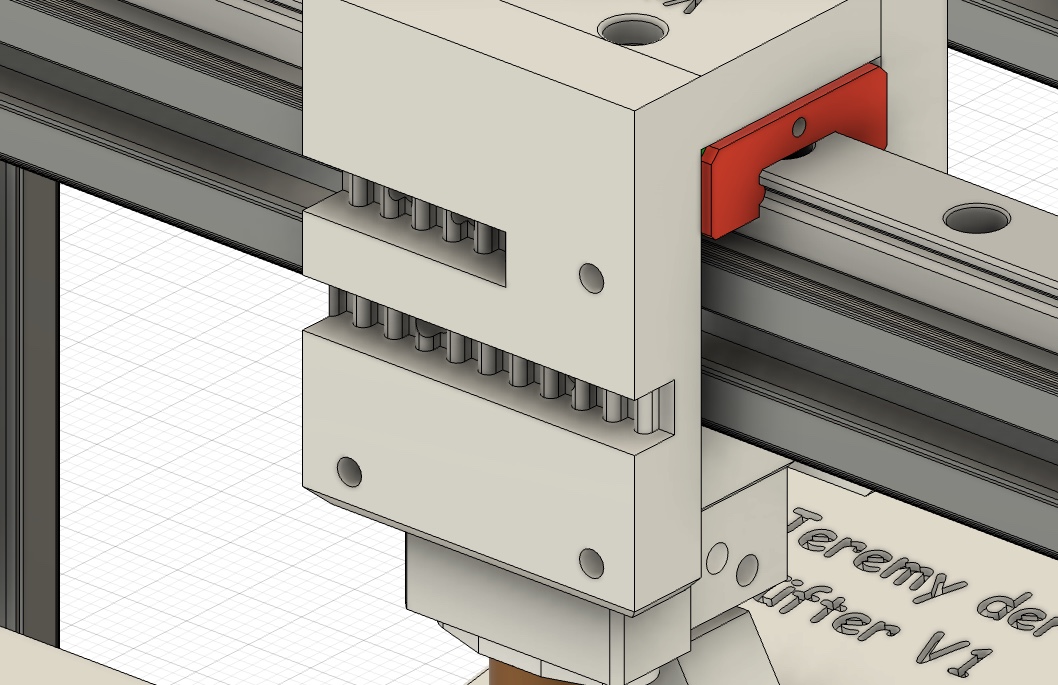
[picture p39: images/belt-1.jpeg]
belt-1


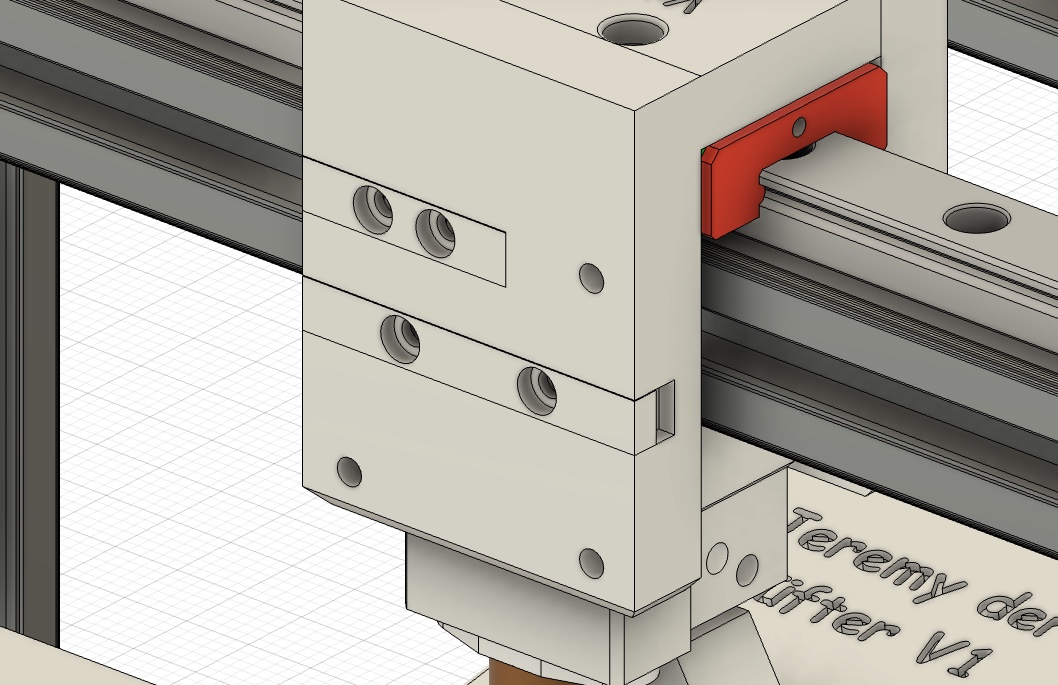
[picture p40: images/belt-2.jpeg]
belt-2


I'll also be using two SKR Mini E3 V3 controller boards to operate the printer with Klipper. I've started making my own 3D printer controller, but that will be implemented in a future project. I'm aware that I'm currently way over budget, but I already have some expensive parts that can be used for the printer. For cost reasons, the laser won't be implemented for now, although it's certainly possible. I will ship the project now because highway is slowly coming to an end, if I have time again I will enclose the printer.

# July 18th - Some last things (3hrs)

I've made mounts for the two controller boards. Which Raspberry Pi I use depends on what arrives in time. Today I also prepared the repository for submitting the project and researched how Klipper works and how to use two controller boards.

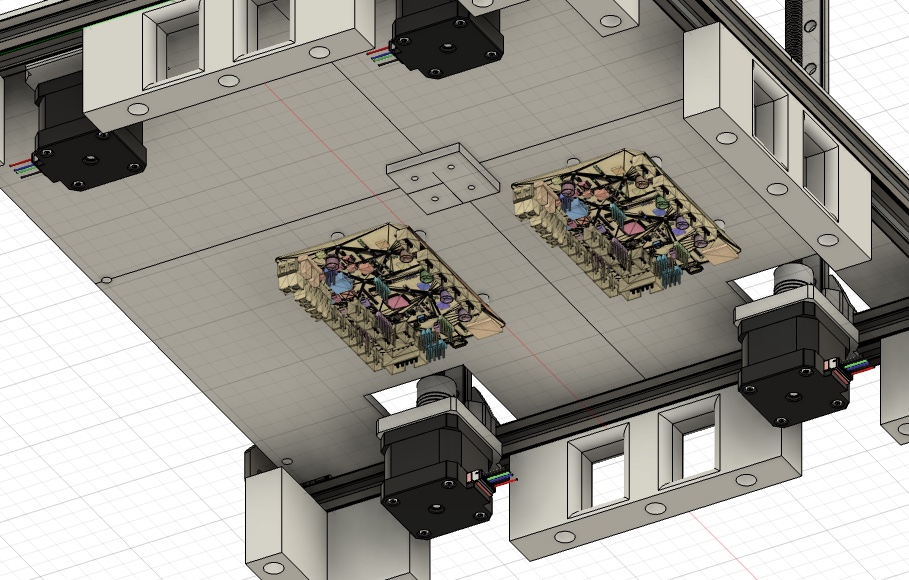
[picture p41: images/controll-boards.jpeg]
controll-boards


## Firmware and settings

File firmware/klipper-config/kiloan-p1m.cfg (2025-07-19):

# To use this config, the firmware should be compiled for the
# STM32G0B1 with a "8KiB bootloader" and USB communication.

# The "make flash" command does not work on the SKR mini E3. Instead,
# after running "make", copy the generated "out/klipper.bin" file to a
# file named "firmware.bin" on an SD card and then restart the SKR
# mini E3 with that SD card.


# The main micro-controller is used for the XY-Axes.
[mcu]
serial: /dev/serial/

# The "zcontroller" will be used for the Z axis.
[mcu zcontroller]
serial: /dev/serial/

# Z Stepper 1
[stepper_z]
step_pin: zcontroller:PB13
dir_pin: !zcontroller:PB12
enable_pin: !zcontroller:PB14
microsteps: 16
rotation_distance: 8
endstop_pin: ^zcontroller:PC0
position_endstop: 0.0
position_max: 250

[tmc2209 stepper_z]
uart_pin: zcontroller:PC11
tx_pin: zcontroller:PC10
uart_address: 0
run_current: 0.580
stealthchop_threshold: 999999

# Z Stepper 2
[stepper_z1]
step_pin: zcontroller:PB10
dir_pin: !zcontroller:PB2
enable_pin: !zcontroller:PB11
microsteps: 16
rotation_distance: 8
endstop_pin: ^zcontroller:PC1
position_endstop: 0.0
position_max: 250

[tmc2209 stepper_z1]
uart_pin: zcontroller:PC11
tx_pin: zcontroller:PC10
uart_address: 2
run_current: 0.580
stealthchop_threshold: 999999

# Z Stepper 3
[stepper_z2]
step_pin: zcontroller:PB0
dir_pin: !zcontroller:PC5
enable_pin: !zcontroller:PB1
microsteps: 16
rotation_distance: 8
endstop_pin: ^zcontroller:PC2
position_endstop: 0.0
position_max: 250

[tmc2209 stepper_z2]
uart_pin: zcontroller:PC11
tx_pin: zcontroller:PC10
uart_address: 1
run_current: 0.580
stealthchop_threshold: 999999

# Z Stepper 4
[stepper_z3]
step_pin: zcontroller:PB3
dir_pin: !zcontroller:PB4
enable_pin: !zcontroller:PD1
microsteps: 16
rotation_distance: 8
endstop_pin: ^zcontroller:PC3
position_endstop: 0.0
position_max: 250

[tmc2209 stepper_z3]
uart_pin: zcontroller:PC11
tx_pin: zcontroller:PC10
uart_address: 3
run_current: 0.580
stealthchop_threshold: 999999

# Bed Heater
[heater_bed]
heater_pin: zcontroller:PC9
sensor_type: EPCOS 100K B57560G104F
sensor_pin: zcontroller:PC4
control: pid
pid_Kp: 54.027
pid_Ki: 0.770
pid_Kd: 948.182
min_temp: 0
max_temp: 120

# Stepper X
[stepper_x]
step_pin: PB13
dir_pin: !PB12
enable_pin: !PB14
microsteps: 16
rotation_distance: 40
endstop_pin: ^PC0
position_endstop: 0
position_max: 235
homing_speed: 50

[tmc2209 stepper_x]
uart_pin: PC11
tx_pin: PC10
uart_address: 0
run_current: 0.580
stealthchop_threshold: 999999

# Stepper Y
[stepper_y]
step_pin: PB10
dir_pin: !PB2
enable_pin: !PB11
microsteps: 16
rotation_distance: 40
endstop_pin: ^PC1
position_endstop: 0
position_max: 235
homing_speed: 50

[tmc2209 stepper_y]
uart_pin: PC11
tx_pin: PC10
uart_address: 2
run_current: 0.580
stealthchop_threshold: 999999

# Extruder
[extruder]
step_pin: PB3
dir_pin: !PB4
enable_pin: !PD1
microsteps: 16
rotation_distance: 33.500
nozzle_diameter: 0.400
filament_diameter: 1.750
heater_pin: PC8
sensor_type: EPCOS 100K B57560G104F
sensor_pin: PA0
control: pid
pid_Kp: 21.527
pid_Ki: 1.063
pid_Kd: 108.982
min_temp: 0
max_temp: 250

[tmc2209 extruder]
uart_pin: PC11
tx_pin: PC10
uart_address: 3
run_current: 0.650

# Hotend Fan
[heater_fan hotend_fan]
pin: PC7

# Part Cooling Fan
[heater_fan part_cooling_fan]
pin: PB15

# Controlboards Fan
[fan]
pin: PC6

[printer]
kinematics: corexy
max_velocity: 300
max_accel: 3000
max_z_velocity: 25
max_z_accel: 30

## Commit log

2025-07-18 add bom
    [bom.csv]
2025-07-19 add hardware files
    [bambu-hotendadapter-V6.stl, bedmount (1).stl, bedmount (2).stl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]
2025-07-19 add Kiloan P1M V1.f3z
    [Kiloan P1M V1.f3z]
2025-07-19 add klipper firmware conf
    [kiloan-p1m.cfg]
